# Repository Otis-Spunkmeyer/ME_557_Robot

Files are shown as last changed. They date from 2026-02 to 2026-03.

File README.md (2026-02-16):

# ME557 Robot

This repository is split into two separate top-level structures:

- Online version (ROS2 + MoveIt): `online/`
- Offline version (Arduino playback): `offline/`

## Online Version

The online stack uses ROS2/MoveIt packages for planning and control:

- `online/src/me557_pen_description`
- `online/src/me557_pen_moveit_config`
- `online/cad/`

## Offline Version

The offline stack runs trajectory playback on Arduino without ROS at runtime:

- `offline/arduino/me557_pen_arduino_ws/me557_pen_arduino_ws.ino`
- `offline/arduino/me557_pen_arduino_ws/ace_trajectory_data.h`
- `offline/arduino/README.md`
- `offline/tools/`

## Quick Start

Build online workspace:

```bash
cd online
source /opt/ros/humble/setup.bash
colcon build
```

Generate offline trajectory header:

```bash
offline/tools/export_offline_ace.sh
```

This export path uses MoveIt planning (`write_ace`) and applies configured
PlanningScene collision objects before planning.

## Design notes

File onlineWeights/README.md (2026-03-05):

# ME557 OnlineWeights — 555 Trajectory Workflow

This workspace is now **555-only** (fixed-speed playback from `trajectory_data.h`).

## Workflow

1. Launch ROS 2 / MoveIt stack:

```bash
cd /home/rosubu/ME_557_Robot/onlineWeights
./launch_rviz.sh
```

2. Trigger planning and export trajectory header:

```bash
cd /home/rosubu/ME_557_Robot/onlineWeights
./trigger_write.sh
```

Each run calls `/board_writer/run_plan` and updates:

- `robotMovements/trajectory_data.h`

3. Flash Arduino sketch:

- `robotMovements/robotMovements.ino`

4. Run from Serial Monitor at `1000000` baud:

- `555` → play `trajectory_data.h`

## Notes

- `pause` flags in `trajectory_data.h` are honored by firmware:
  - `pause=1`: full stop + contact dwell
  - `pause=2`: full stop (corner settle), no dwell
  - `pause=3`: full stop + user pause dwell
- Current firmware uses synchronized Dynamixel start (`REG_WRITE + ACTION`) for better multi-joint coordination.

## Key files

- `robotMovements/robotMovements.ino`
- `robotMovements/trajectory_data.h`
- `src/me557_pen_description/me557_pen_description/write_on_board.py`
- `src/me557_pen_moveit_config/config/write_on_board.yaml`

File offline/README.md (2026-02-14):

# ME557 Offline (Arduino)

This folder is the offline workspace.

Key paths:

- `arduino/` firmware and trajectory header.
- `tools/` export and calibration scripts.
- `individualMove.ino` helper sketch.

Entry guide:

- `arduino/README.md`

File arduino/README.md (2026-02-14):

# ME557 Arduino Offline Playback

This folder runs the pen path on Arduino without ROS at runtime.

## Files

- `me557_pen_arduino_ws/me557_pen_arduino_ws.ino`: main firmware.
- `me557_pen_arduino_ws/ace_trajectory_data.h`: exported MoveIt trajectory points.
- `../tools/export_moveit_joint_trajectory.py`: captures trajectory from MoveIt and writes header.
- `../tools/compute_moveit_calibration.py`: computes `MOVEIT_HOME_RAD` and `MOVEIT_DIR_SIGN`.

## Export ACE trajectory

From workspace root (`ME557_pen_arduino_ws`) with MoveIt running:

```bash
source /opt/ros/humble/setup.bash
source install/setup.bash
ROS_DOMAIN_ID=57 ROS_LOCALHOST_ONLY=1 \
python3 tools/export_moveit_joint_trajectory.py \
  --run-write-ace \
  --output arduino/me557_pen_arduino_ws/ace_trajectory_data.h
```

One-command offline export (launches MoveIt, exports, validates summary, then stops):

```bash
tools/export_offline_ace.sh
```

Useful options:

```bash
# Strict 14" x 14" tip bounds on XZ
tools/export_offline_ace.sh \
  --workspace-enforce-x-bounds true \
  --workspace-x-min -0.1778 \
  --workspace-x-max 0.1778 \
  --workspace-z-min 0.0 \
  --workspace-z-max 0.3556

# Floor-only Z constraint, unbounded X for tip requests
tools/export_offline_ace.sh \
  --workspace-enforce-x-bounds false \
  --workspace-z-min 0.0 \
  --workspace-z-max 10.0
```

## Arduino commands

- `555`: play exported trajectory.
- `777`: per-joint ROM sweep.
- `888`: full ROM showcase.
- `901`: print current logical/physical angles and estimated MoveIt radians.
- `902`: per-joint sign/home calibration helper.

## Calibration example

1. Send `901` and record logical angles for IDs `[1,2,4,5,6]`.
2. Send `902` for each MoveIt joint index `1..5`, choose sign direction.
3. Collect synchronized values from one pose:

- MoveIt rad (5 joints), example:
```text
0.00698 5.55596 -0.66950 0.18387 0.00524
```
- Logical deg from `901`, example:
```text
180.4 179.2 181.1 179.7 180.3
```
- Signs from `902`, example:
```text
1 1 -1 1 1
```

4. Compute constants:

```bash
python3 tools/compute_moveit_calibration.py \
  --moveit-rad 0.00698 5.55596 -0.66950 0.18387 0.00524 \
  --logical-deg 180.4 179.2 181.1 179.7 180.3 \
  --sign 1 1 -1 1 1
```

5. Paste output into `me557_pen_arduino_ws/me557_pen_arduino_ws.ino` and reflash.

## Notes

- `901` and `902` print values only; they do not save to EEPROM or source.
- Keep MoveIt and hardware values from the same pose.
- If one joint is inverted, flip only that joint sign and recompute home.

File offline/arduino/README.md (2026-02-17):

# ME557 Arduino Offline Playback

This folder is the offline ME557 firmware and trajectory data.

Repository layout:

- `online/`: ROS2 + MoveIt workspace.
- `offline/`: Arduino firmware plus offline export/calibration tools.

## Files

- `me557_pen_arduino_ws/me557_pen_arduino_ws.ino`: main firmware.
- `me557_pen_arduino_ws/ace_trajectory_data.h`: exported MoveIt trajectory points.
- `../tools/export_moveit_joint_trajectory.py`: captures trajectory from MoveIt and writes header.
- `../tools/compute_moveit_calibration.py`: computes `MOVEIT_HOME_RAD` and `MOVEIT_DIR_SIGN`.
- `../tools/generate_offline_ace_ik_trajectory.py`: legacy IK-only debug exporter (no collision-aware planning).

## Export ACE trajectory

From repo root (`ME557_pen_arduino_ws`) with online workspace already built:

```bash
source /opt/ros/humble/setup.bash
source online/install/setup.bash
ROS_DOMAIN_ID=57 ROS_LOCALHOST_ONLY=1 \
python3 offline/tools/export_moveit_joint_trajectory.py \
  --run-write-ace \
  --output offline/arduino/me557_pen_arduino_ws/ace_trajectory_data.h
```

One-command offline export (launches MoveIt, exports, validates summary, then stops):

```bash
offline/tools/export_offline_ace.sh
```

`export_offline_ace.sh` runs `write_ace` in plan-only mode, captures planned
time-parameterized joint motion, and applies configured PlanningScene collision
objects (board/table) before planning.

Useful options:

```bash
# Strict 14" x 14" tip bounds on XZ
offline/tools/export_offline_ace.sh \
  --workspace-enforce-x-bounds true \
  --workspace-x-min -0.1778 \
  --workspace-x-max 0.1778 \
  --workspace-z-min 0.0 \
  --workspace-z-max 0.3556

# Floor-only Z constraint, unbounded X for tip requests
offline/tools/export_offline_ace.sh \
  --workspace-enforce-x-bounds false \
  --workspace-z-min 0.0 \
  --workspace-z-max 10.0

# Override board collision object used by planning scene setup
offline/tools/export_offline_ace.sh \
  --scene-board-center-x 0.415 \
  --scene-board-center-y 0.000 \
  --scene-board-center-z 0.230 \
  --scene-board-size-x 0.01 \
  --scene-board-size-y 0.45 \
  --scene-board-size-z 0.42

# Rotate ACE path in board plane (+90 deg CCW about Z)
offline/tools/export_offline_ace.sh \
  --semantic-yaw-deg 90.0
```

## Arduino commands

- `555`: play exported trajectory.
- `777`: per-joint ROM sweep.
- `888`: full ROM showcase.
- `901`: print current logical/physical angles and estimated MoveIt radians.
- `902`: per-joint sign/home calibration helper.

## Calibration example

1. Send `901` and record logical angles for IDs `[1,2,4,5,6]`.
2. Send `902` for each MoveIt joint index `1..5`, choose sign direction.
3. Collect synchronized values from one pose:

- MoveIt rad (5 joints), example:
```text
0.00698 5.55596 -0.66950 0.18387 0.00524
```
- Logical deg from `901`, example:
```text
180.4 179.2 181.1 179.7 180.3
```
- Signs from `902`, example:
```text
1 1 -1 1 1
```

4. Compute constants:

```bash
python3 offline/tools/compute_moveit_calibration.py \
  --moveit-rad 0.00698 5.55596 -0.66950 0.18387 0.00524 \
  --logical-deg 180.4 179.2 181.1 179.7 180.3 \
  --sign 1 1 -1 1 1
```

5. Paste output into `me557_pen_arduino_ws/me557_pen_arduino_ws.ino` and reflash.

## Notes

- `901` and `902` print values only; they do not save to EEPROM or source.
- Keep MoveIt and hardware values from the same pose.
- If one joint is inverted, flip only that joint sign and recompute home.

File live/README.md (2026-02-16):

# ME557 Online (ROS2 + MoveIt)

This folder is the online workspace.

Key paths:

- `src/me557_pen_description`
- `src/me557_pen_moveit_config`
- `cad/`

Build and run:

```bash
cd online
source /opt/ros/humble/setup.bash
colcon build
source install/setup.bash
ros2 launch me557_pen_moveit_config demo.launch.py
```

Run `write_ace` online with the same PlanningScene collision setup used by offline export:

```bash
ros2 launch me557_pen_moveit_config write_ace_online.launch.py use_rviz:=false
```

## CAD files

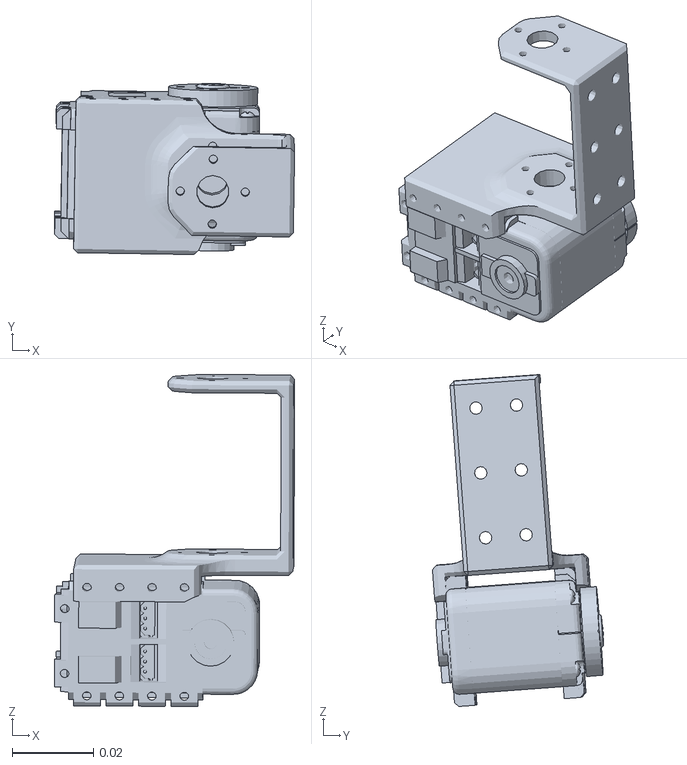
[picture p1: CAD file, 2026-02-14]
live/cad/Robot Assembly.SLDASM/meshes/Link4_Wr.STL
0.0591 x 0.0421 x 0.0817

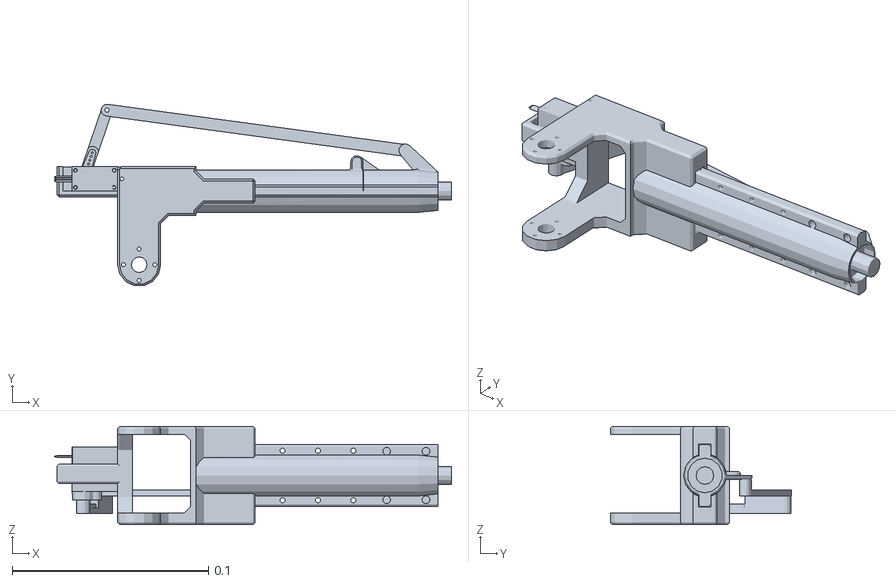
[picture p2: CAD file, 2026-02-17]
onlineWeights/src/me557_pen_description/meshes/Link6.STL
0.202 x 0.0924 x 0.05

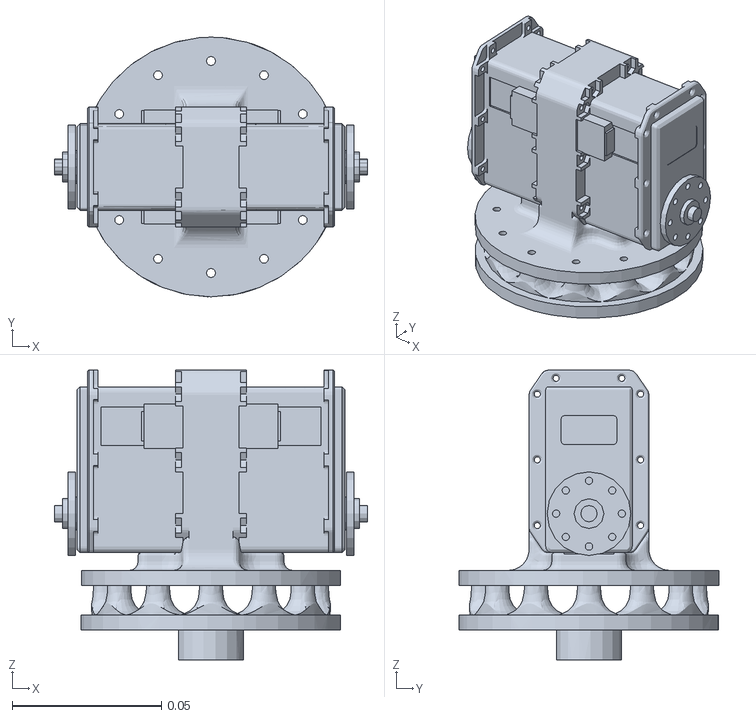
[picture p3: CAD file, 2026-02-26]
simple_with_weights_v1/meshes/RotatingBaseLink.STL
0.105 x 0.087 x 0.0971

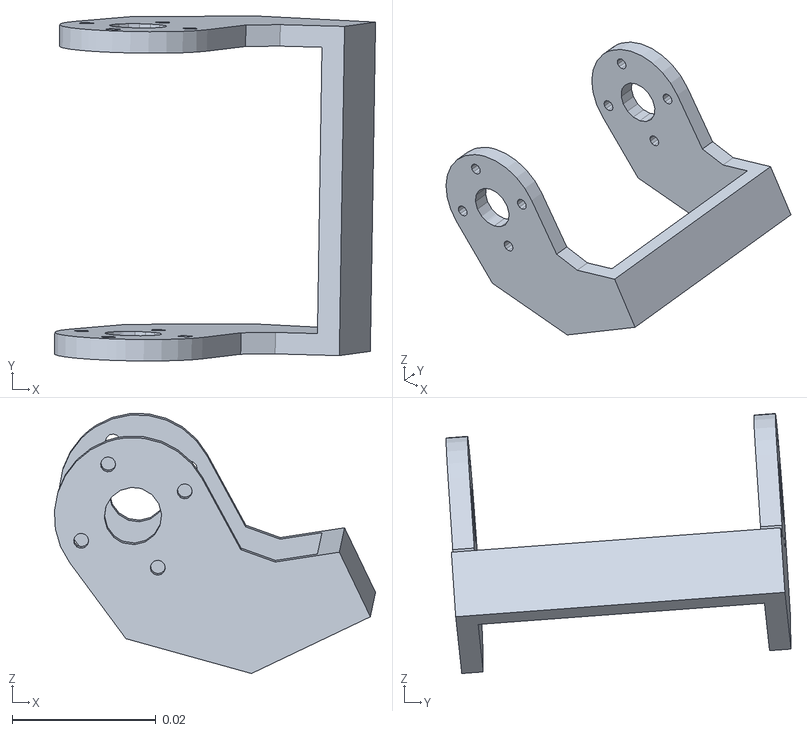
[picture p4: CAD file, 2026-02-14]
live/cad/Robot Assembly.SLDASM/meshes/Link5_EE.STL
0.0447 x 0.0481 x 0.0362

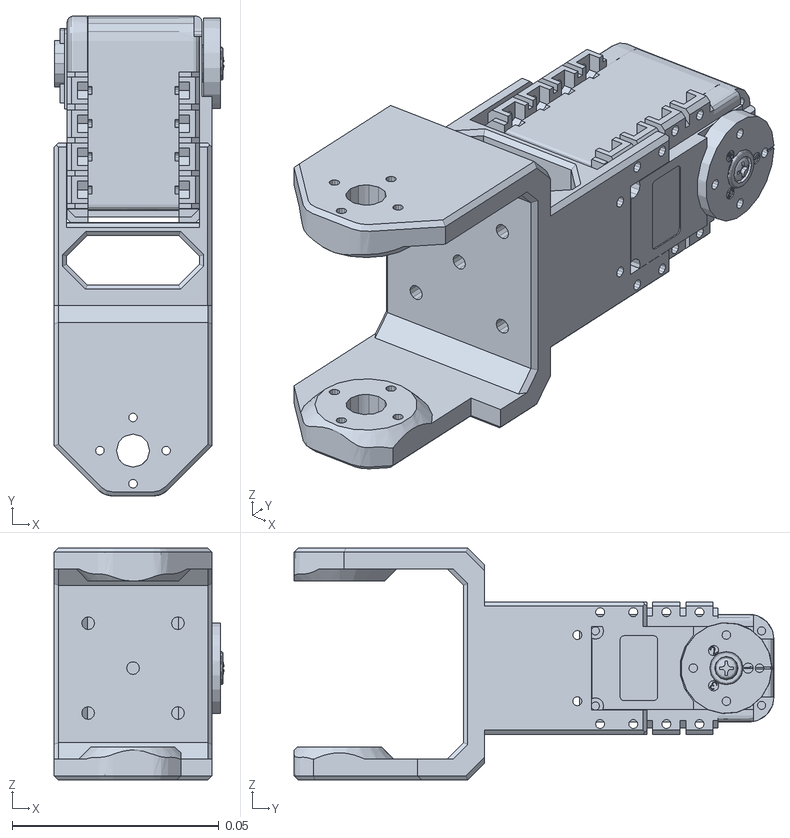
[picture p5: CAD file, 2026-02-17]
onlineWeights/src/me557_pen_description/meshes/Link4.STL
0.041 x 0.116 x 0.056

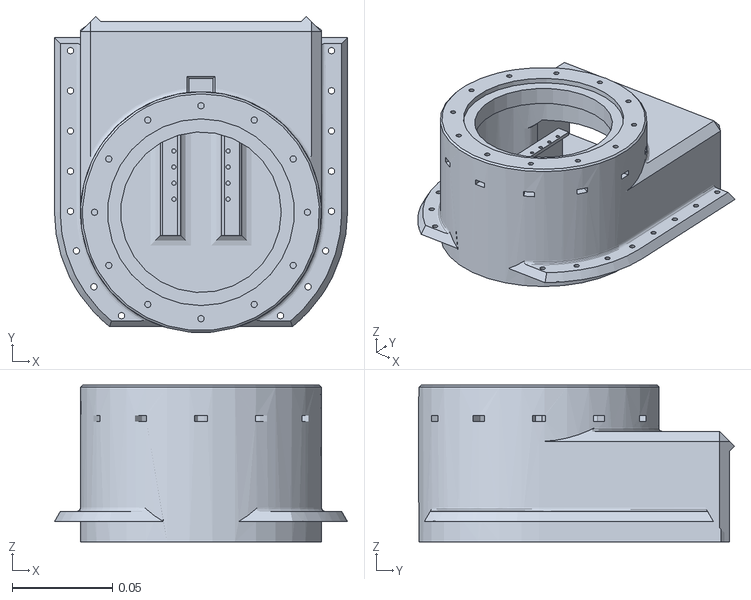
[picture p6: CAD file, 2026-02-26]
simple_with_weights_v1/meshes/FixedBase.STL
0.146 x 0.157 x 0.078

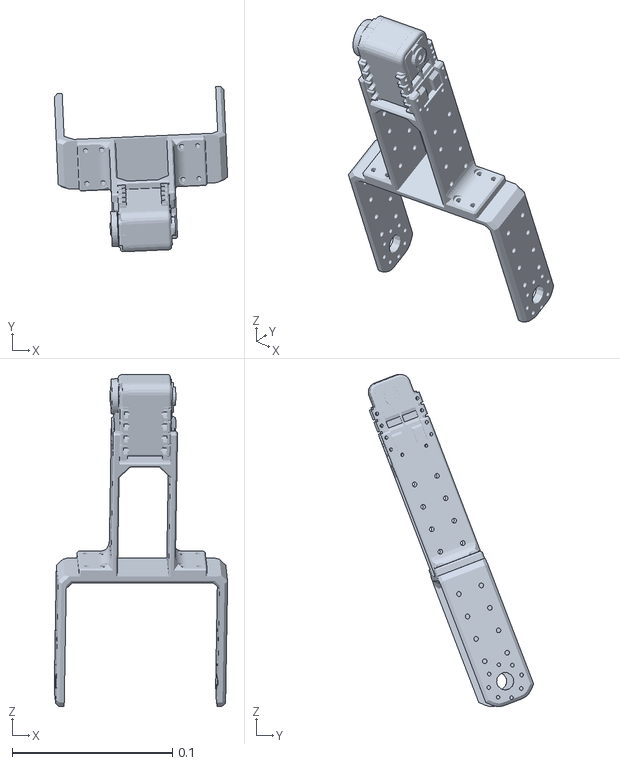
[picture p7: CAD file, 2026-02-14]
live/cad/Robot Assembly.SLDASM/meshes/Link2_R.STL
0.108 x 0.103 x 0.207

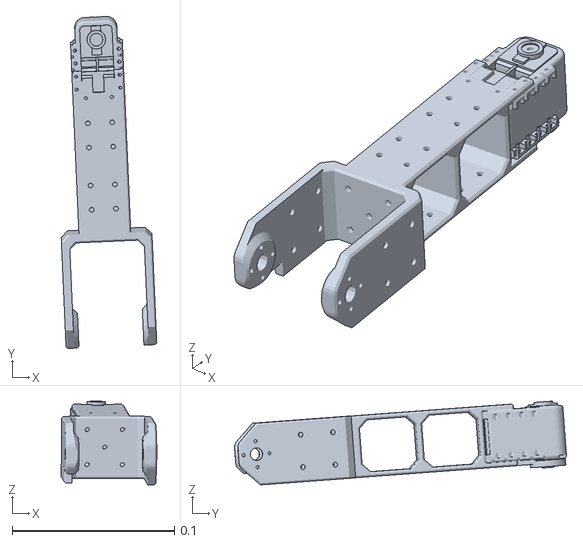
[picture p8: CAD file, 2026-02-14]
live/cad/Robot Assembly.SLDASM/meshes/Link3_Elb.STL
0.0589 x 0.205 x 0.0517

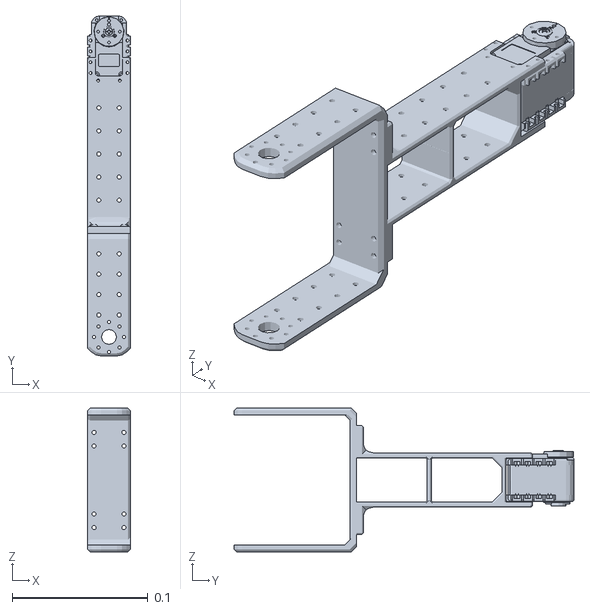
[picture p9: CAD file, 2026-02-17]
onlineWeights/src/me557_pen_description/meshes/Link3_R.STL
0.032 x 0.25 x 0.106

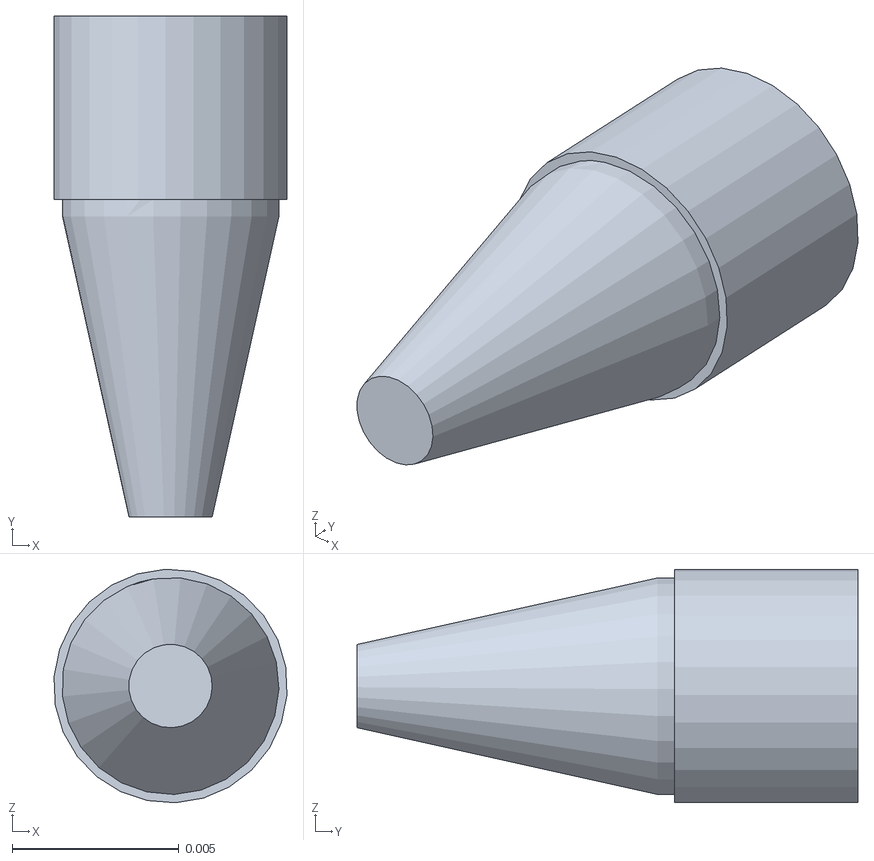
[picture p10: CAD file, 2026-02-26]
simple_with_weights_v1/meshes/PenTipLink.STL
0.00698 x 0.015 x 0.00699

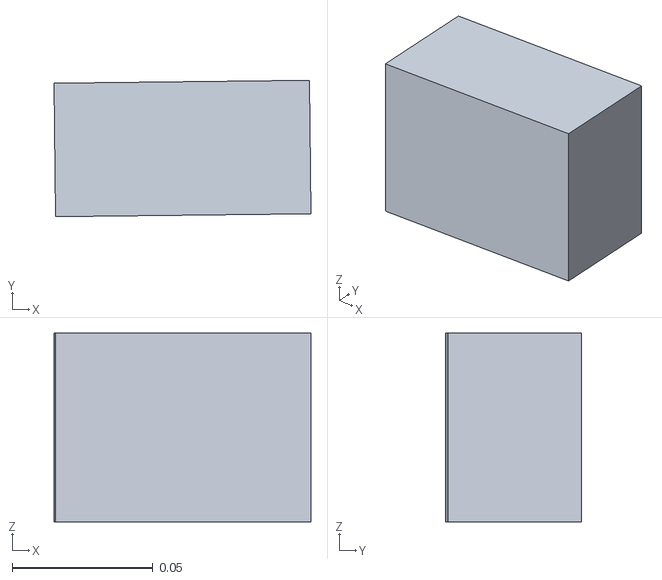
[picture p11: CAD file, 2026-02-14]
live/cad/Robot Assembly.SLDASM/meshes/Link1.STL
0.0915 x 0.0485 x 0.0671

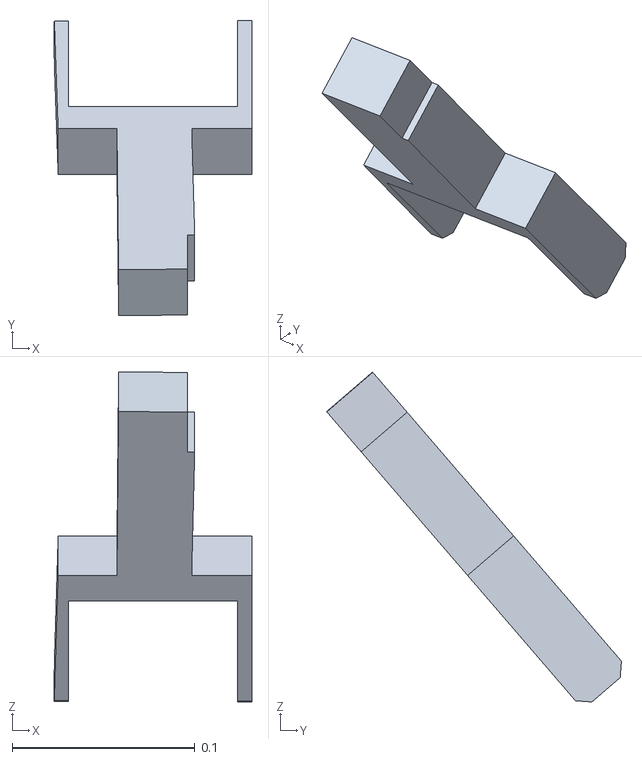
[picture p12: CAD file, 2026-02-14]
live/cad/Robot Assembly.SLDASM/meshes/Link2_L.STL
0.108 x 0.161 x 0.181

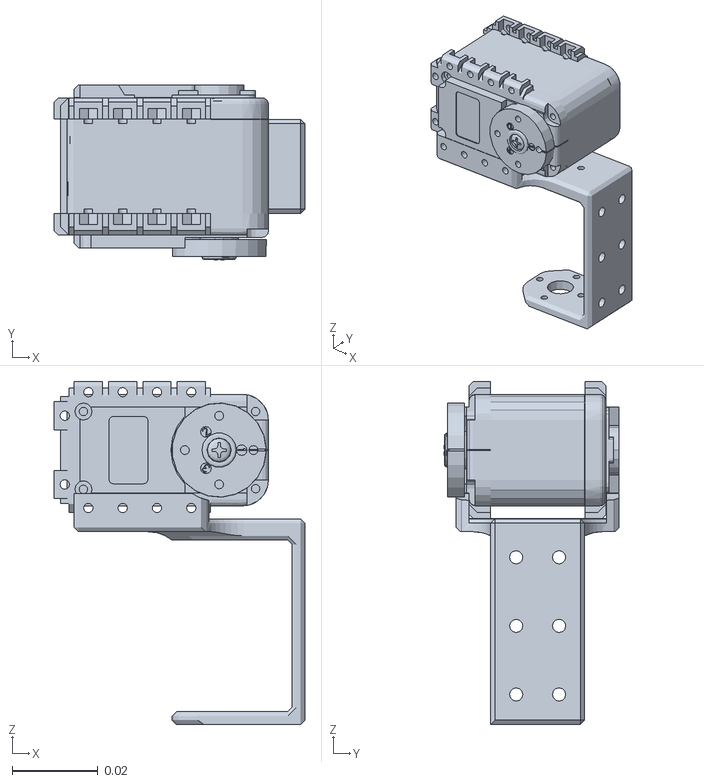
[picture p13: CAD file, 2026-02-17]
onlineWeights/src/me557_pen_description/meshes/Link5.STL
0.0585 x 0.0409 x 0.08

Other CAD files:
onlineWeights/src/me557_pen_description/meshes/Link1.STL
simple_with_weights_v1/meshes/ElbowLink.STL
simple_with_weights_v1/meshes/PenLink.STL
simple_with_weights_v1/meshes/WristLink.STL
live/cad/Robot Assembly.SLDASM/meshes/Link4.STL
live/cad/Robot Assembly.SLDASM/meshes/Link5.STL
live/cad/Robot Assembly.SLDASM/meshes/Link6.STL
live/cad/Robot Assembly.SLDASM/meshes/Pen_tip.STL
live/cad/Robot Assembly.SLDASM/meshes/base_link.STL
onlineWeights/src/me557_pen_description/meshes/Pen_tip.STL
onlineWeights/src/me557_pen_description/meshes/base_link.STL
simple_with_weights_v1/meshes/ShoulderLink.STL

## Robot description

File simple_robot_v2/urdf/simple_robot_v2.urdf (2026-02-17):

<?xml version="1.0" encoding="utf-8"?>
<!-- This URDF was automatically created by SolidWorks to URDF Exporter! Originally created by Stephen Brawner (brawner@gmail.com) 
     Commit Version: 1.6.0-4-g7f85cfe  Build Version: 1.6.7995.38578
     For more information, please see http://wiki.ros.org/sw_urdf_exporter -->
<robot name="simple_robot_v2">
  <link name="FixedBase">
    <inertial>
      <origin xyz="-0.008662 6.915E-09 0.034203" rpy="0 0 0" />
      <mass value="0.49574" />
      <inertia ixx="0.0011079" ixy="1.4362E-10" ixz="-3.7324E-05" iyy="0.0011344" iyz="-8.7399E-11" izz="0.0016547" />
    </inertial>
    <visual>
      <origin xyz="0 0 0" rpy="0 0 0" />
      <geometry>
        <mesh filename="package://simple_robot_v2/meshes/FixedBase.STL" />
      </geometry>
      <material name="">
        <color rgba="0.79216 0.81961 0.93333 1" />
      </material>
    </visual>
    <collision>
      <origin xyz="0 0 0" rpy="0 0 0" />
      <geometry>
        <mesh filename="package://simple_robot_v2/meshes/FixedBase.STL" />
      </geometry>
    </collision>
  </link>
  <link name="RotatingBaseLink">
    <inertial>
      <origin xyz="-1.0615E-08 1.3952E-09 0.05044" rpy="0 0 0" />
      <mass value="0.24905" />
      <inertia ixx="0.00030195" ixy="6.1355E-07" ixz="2.7299E-11" iyy="0.0002068" iyz="4.0363E-11" izz="0.00019603" />
    </inertial>
    <visual>
      <origin xyz="0 0 0" rpy="0 0 0" />
      <geometry>
        <mesh filename="package://simple_robot_v2/meshes/RotatingBaseLink.STL" />
      </geometry>
      <material name="">
        <color rgba="0.50196 0.50196 1 1" />
      </material>
    </visual>
    <collision>
      <origin xyz="0 0 0" rpy="0 0 0" />
      <geometry>
        <mesh filename="package://simple_robot_v2/meshes/RotatingBaseLink.STL" />
      </geometry>
    </collision>
  </link>
  <joint name="RotatingBaseJoint" type="revolute">
    <origin xyz="0 0 0.05" rpy="0 0 0" />
    <parent link="FixedBase" />
    <child link="RotatingBaseLink" />
    <axis xyz="0 0 -1" />
    <limit lower="2.0944" upper="3.8397" effort="0" velocity="0" />
  </joint>
  <link name="ShoulderLink">
    <inertial>
      <origin xyz="1.5118E-06 0.13231 0.0003468" rpy="0 0 0" />
      <mass value="0.12701" />
      <inertia ixx="0.00076308" ixy="1.1682E-08" ixz="8.706E-09" iyy="0.00010667" iyz="-3.3149E-06" izz="0.00067538" />
    </inertial>
    <visual>
      <origin xyz="0 0 0" rpy="0 0 0" />
      <geometry>
        <mesh filename="package://simple_robot_v2/meshes/ShoulderLink.STL" />
      </geometry>
      <material name="">
        <color rgba="0.79216 0.81961 0.93333 1" />
      </material>
    </visual>
    <collision>
      <origin xyz="0 0 0" rpy="0 0 0" />
      <geometry>
        <mesh filename="package://simple_robot_v2/meshes/ShoulderLink.STL" />
      </geometry>
    </collision>
  </link>
  <joint name="ShoulderJoint" type="revolute">
    <origin xyz="0 0 0.049" rpy="1.5708 0 0.0064475" />
    <parent link="RotatingBaseLink" />
    <child link="ShoulderLink" />
    <axis xyz="0 0 1" />
    <limit lower="2.0944" upper="4.18879" effort="0" velocity="0" />
  </joint>
  <link name="ElbowLink">
    <inertial>
      <origin xyz="0.00036697 0.055834 -0.0004101" rpy="0 0 0" />
      <mass value="0.083206" />
      <inertia ixx="9.1587E-05" ixy="-1.7788E-06" ixz="-2.7941E-07" iyy="2.5642E-05" iyz="2.0881E-06" izz="8.5875E-05" />
    </inertial>
    <visual>
      <origin xyz="0 0 0" rpy="0 0 0" />
      <geometry>
        <mesh filename="package://simple_robot_v2/meshes/ElbowLink.STL" />
      </geometry>
      <material name="">
        <color rgba="0.79216 0.81961 0.93333 1" />
      </material>
    </visual>
    <collision>
      <origin xyz="0 0 0" rpy="0 0 0" />
      <geometry>
        <mesh filename="package://simple_robot_v2/meshes/ElbowLink.STL" />
      </geometry>
    </collision>
  </link>
  <joint name="ElbowJoint" type="revolute">
    <origin xyz="0 0.2247 0.00104" rpy="0 0 0" />
    <parent link="ShoulderLink" />
    <child link="ElbowLink" />
    <axis xyz="0 0 1" />
    <limit lower="1.309" upper="5.06145" effort="0" velocity="0" />
  </joint>
  <link name="WristLink">
    <inertial>
      <origin xyz="-0.010184 -0.0007354 0.034941" rpy="0 0 0" />
      <mass value="0.053757" />
      <inertia ixx="1.8975E-05" ixy="3.4773E-08" ixz="4.7677E-06" iyy="2.5817E-05" iyz="2.3142E-07" izz="1.7812E-05" />
    </inertial>
    <visual>
      <origin xyz="0 0 0" rpy="0 0 0" />
      <geometry>
        <mesh filename="package://simple_robot_v2/meshes/WristLink.STL" />
      </geometry>
      <material name="">
        <color rgba="0.9098 0.44314 0.031373 1" />
      </material>
    </visual>
    <collision>
      <origin xyz="0 0 0" rpy="0 0 0" />
      <geometry>
        <mesh filename="package://simple_robot_v2/meshes/WristLink.STL" />
      </geometry>
    </collision>
  </link>
  <joint name="WristJoint" type="revolute">
    <origin xyz="0.00108 0.0935 -0.001" rpy="1.5708 0 1.5708" />
    <parent link="ElbowLink" />
    <child link="WristLink" />
    <axis xyz="0 0 -1" />
    <limit lower="2.618" upper="4.5379" effort="0" velocity="0" />
  </joint>
  <link name="PenLink">
    <inertial>
      <origin xyz="0.048807 0.037513 -0.0021456" rpy="0 0 0" />
      <mass value="0.081357" />
      <inertia ixx="2.8223E-05" ixy="-3.704E-06" ixz="-2.8914E-06" iyy="0.00024631" iyz="5.6477E-07" izz="0.00024327" />
    </inertial>
    <visual>
      <origin xyz="0 0 0" rpy="0 0 0" />
      <geometry>
        <mesh filename="package://simple_robot_v2/meshes/PenLink.STL" />
      </geometry>
      <material name="">
        <color rgba="0.50196 1 0.50196 1" />
      </material>
    </visual>
    <collision>
      <origin xyz="0 0 0" rpy="0 0 0" />
      <geometry>
        <mesh filename="package://simple_robot_v2/meshes/PenLink.STL" />
      </geometry>
    </collision>
  </link>
  <joint name="PenJoint" type="revolute">
    <origin xyz="0 -0.001 0.041" rpy="1.5708 0 0" />
    <parent link="WristLink" />
    <child link="PenLink" />
    <axis xyz="0 0 1" />
    <limit lower="1.4835" upper="3.8397" effort="0" velocity="0" />
  </joint>
  <link name="PenTipLink">
    <inertial>
      <origin xyz="1.2388E-08 -1.5096E-08 -0.0095156" rpy="0 0 0" />
      <mass value="0.00038082" />
      <inertia ixx="6.068E-09" ixy="2.1976E-14" ixz="1.8806E-14" iyy="6.0679E-09" iyz="-2.2912E-14" izz="1.8923E-09" />
    </inertial>
    <visual>
      <origin xyz="0 0 0" rpy="0 0 0" />
      <geometry>
        <mesh filename="package://simple_robot_v2/meshes/PenTipLink.STL" />
      </geometry>
      <material name="">
        <color rgba="0.50196 1 0.50196 1" />
      </material>
    </visual>
    <collision>
      <origin xyz="0 0 0" rpy="0 0 0" />
      <geometry>
        <mesh filename="package://simple_robot_v2/meshes/PenTipLink.STL" />
      </geometry>
    </collision>
  </link>
  <joint name="PenTipJoint" type="continuous">
    <origin xyz="0.17403 0.0375 -0.00098" rpy="1.5708 -1.5643 1.5708" />
    <parent link="PenLink" />
    <child link="PenTipLink" />
    <axis xyz="-0.45244 0.63071 -0.63047" />
  </joint>
</robot>

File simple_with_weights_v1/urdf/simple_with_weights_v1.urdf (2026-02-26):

<?xml version="1.0" encoding="utf-8"?>
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
<robot name="simple_with_weights_v1">
  <link name="FixedBase">
    <inertial>
      <origin xyz="6.915E-09 0.008662 0.034203" rpy="0 0 0" />
      <mass value="0.49574" />
      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
    </inertial>
    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
  </link>
  <link name="RotatingBaseLink">
    <inertial>
      <origin xyz="1.7639E-09 1.0285E-08 0.05044" rpy="0 0 0" />
      <mass value="0.36361" />
      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
    </inertial>
    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
  </link>
  <joint name="RotatingBaseJoint" type="revolute">
    <origin xyz="0 0 0.05" rpy="0 0 0" />
    <parent link="FixedBase" />
    <child link="RotatingBaseLink" />
    <axis xyz="0 0 -1" />
    <limit lower="0" upper="0" effort="0.15" velocity="0" />
  </joint>
  <link name="ShoulderLink">
    <inertial>
      <origin xyz="-0.000346804399082955 -1.51178301074372E-06 0.132307785392207" rpy="0 0 0" />
      <mass value="0.138435482736122" />
      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
    </inertial>
    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
  </link>
  <joint name="ShoulderJoint" type="revolute">
    <origin xyz="0 0 0.049" rpy="0 0 0" />
    <parent link="RotatingBaseLink" />
    <child link="ShoulderLink" />
    <axis xyz="-1 0 0" />
    <limit lower="0" upper="0" effort="8" velocity="0" />
  </joint>
  <link name="ElbowLink">
    <inertial>
      <origin xyz="0.000410096249429826 -0.000366974946254552 0.0558340165515793" rpy="0 0 0" />
      <mass value="0.0915265999893292" />
      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
    </inertial>
    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
  </link>
  <joint name="ElbowJoint" type="revolute">
    <origin xyz="-0.00104 0 0.2247" rpy="0 0 0" />
    <parent link="ShoulderLink" />
    <child link="ElbowLink" />
    <axis xyz="-1 0 0" />
    <limit lower="0" upper="0" effort="0.15" velocity="0" />
  </joint>
  <link name="WristLink">
    <inertial>
      <origin xyz="0.00073541 -0.034941 -0.010184" rpy="0 0 0" />
      <mass value="0.069884" />
      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
    </inertial>
    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
  </link>
  <joint name="WristJoint" type="revolute">
    <origin xyz="0.001 -0.00108 0.0935" rpy="0 0 0" />
    <parent link="ElbowLink" />
    <child link="WristLink" />
    <axis xyz="0 1 0" />
    <limit lower="0" upper="0" effort="0.15" velocity="0" />
  </joint>
  <link name="PenLink">
    <inertial>
      <origin xyz="-0.0021456 -0.037513 0.048807" rpy="0 0 0" />
      <mass value="0.071594" />
      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
    </inertial>
    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
  </link>
  <joint name="PenJoint" type="revolute">
    <origin xyz="0.001 -0.041 0" rpy="0 0 0" />
    <parent link="WristLink" />
    <child link="PenLink" />
    <axis xyz="1 0 0" />
    <limit lower="0" upper="0" effort="0.15" velocity="0" />
  </joint>
  <link name="PenTipLink">
    <inertial>
      <origin xyz="-1.2671E-08 0.0095156 1.4864E-08" rpy="0 0 0" />
      <mass value="0.00049506" />
      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
    </inertial>
    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
  </link>
  <joint name="PenTipJoint" type="continuous">
    <origin xyz="-0.00098 -0.0375 0.17403" rpy="-1.5708 0 -0.5042" />
    <parent link="PenLink" />
    <child link="PenTipLink" />
    <axis xyz="-0.70084 0.63047 0.33365" />
  </joint>
</robot>

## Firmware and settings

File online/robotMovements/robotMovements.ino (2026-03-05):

#include <Dynamixel2Arduino.h>
#include <Servo.h>
#include "trajectory_data.h"
#include "moveItData.h"

#define DXL_SERIAL Serial1
#define PC_SERIAL  Serial

using namespace ControlTableItem;

Dynamixel2Arduino d2a(DXL_SERIAL);

// PWM hobby servo on pin 3 — controlled as ID 7
#define PEN_SERVO_PIN      3
#define PEN_SERVO_HOME_DEG 90
Servo penServo;

// =============================================================================
// CONFIGURATION — edit these values to tune robot behaviour
// =============================================================================
const int   HOME_SPEED         = 15;    // Speed when homing (seq 100 / startup)
const int   MANUAL_SPEED       = 15;    // Speed in manual ID control mode
const int   TRAJECTORY_SPEED   = 8;     // Speed during trajectory streaming — slow so moves take LONGER than the interval
const int   ACCEL_SMOOTH       = 15;    // Profile acceleration — moderate ramp, allows smooth blending

// Trajectory playback
// During a drawing segment keyframes are STREAMED at this interval.  The servo
// receives the next goal position while still moving toward the previous one;
// its internal velocity profile blends smoothly through each waypoint.
// Tune so the interval roughly matches how long each inter-keyframe move takes
// at TRAJECTORY_SPEED — too short and servos lag; too long and they over-stop.
const unsigned long  KEYFRAME_INTERVAL_MS = 30;  // ms between streamed keyframes
// Extra settle time (ms) after all servos report stopped at a pause boundary.
const unsigned long  SETTLE_MS            = 50;
// Dwell time (ms) applied at draw<->travel boundary keyframes (pause flag).
const unsigned long  RETRACT_PAUSE_MS     = 500;
// Timeout (ms) for waitForMotionComplete — safety valve so a stalled servo
// does not hang the sketch forever.
const unsigned long  MOTION_TIMEOUT_MS    = 8000;

// Per-servo PID overrides for servo 1 (base rotation).
// This servo has an extra bearing load causing overshoot oscillation.
// Lowering P reduces the aggressiveness of correction (less overshoot).
// Adding D adds velocity-based damping that actively kills oscillation.
// These only apply to XM/XH servos; AX-12 uses compliance slope instead.
//   XM/XH defaults: P=800, I=0, D=0
//   AX-12: compliance slope used instead (see applySmoothing)
const int SERVO1_P_GAIN          = 400;   // < 800 default: reduce overshoot aggressiveness
const int SERVO1_D_GAIN          = 400;   // > 0 default: add damping to kill oscillation
const int SERVO1_I_GAIN          = 0;     // keep at 0 — I gain adds wind-up, worsens oscillation
const int SERVO1_AX12_SLOPE      = 96;    // AX-12 only: softer compliance = less oscillation

// Per-servo compliance overrides for servo 4 (AX-12 with worst moment arm).
// High load at a disadvantaged moment arm causes the servo to hunt:
// it overshoots slightly, brakes, overshoots the other way, repeat.
//
// Slope controls the torque ramp around the target (higher = softer spring).
//   Valid values: 2, 4, 8, 16, 32, 64, 128
//   Higher slope = gentler approach = less snap-back jitter, but slightly
//   less positional stiffness.  Start at 128 and tighten down if needed.
//
// Margin is the dead-zone (raw units) where zero torque is applied.
//   0 = fight every tiny error (causes buzzing under load)
//   2-4 = ignore sub-degree noise (stops the hunting loop)
//   Don't go above ~5 or positional accuracy visibly degrades.
const int SERVO4_AX12_SLOPE          = 64;  // middle ground: fast enough, soft enough
const int SERVO4_AX12_MARGIN         = 3;   // wider dead-zone kills resonance-exciting micro-hunt
// Servo 4 gets its own trajectory speed, higher than the global setting.
// At speed 8 it lacks torque authority against gravity when the arm is
// extended — the joint lags, then snaps/bounces to catch up.
// A higher speed keeps torque output high enough to move decisively.
const int SERVO4_TRAJECTORY_SPEED    = 15;
// =============================================================================

// Per-motor calibration, mapping physical to logical angle ranges and offsets
struct RobotMotor {
  uint8_t  id;            // Dynamixel ID
  float    physicalOffset; // Physical zero offset used to align to logical 180deg
  float    lowerLimit;    // Logical lower limit (deg)
  float    upperLimit;    // Logical upper limit (deg)
  uint16_t modelNumber;   // Cached on first use — avoids a bus read every move
};

RobotMotor motors[] = {
  {1, 150.0, 120.0, 220.0, 0},
  {2, 170.0, 120.0, 240.0, 0},  // MX-64A — Protocol 1.0, model 310
  {3, 187.0, 120.0, 240.0, 0},  // MX-64A — Protocol 1.0, model 310
  {4, 150.0,  40.0, 240.0, 0},
  {5, 150.0, 100.0, 260.0, 0},
  {6, 150.0, 140.0, 300.0, 0}
};


const uint8_t MOVEIT_TO_SERVO_ID[5] = {1, 2, 4, 5, 6};

// MoveIt (radians) <-> logical (degrees) calibration.
// Tune once on hardware; keep consistent with the MoveIt export tool.
const float MOVEIT_HOME_RAD[5] = {0.0f, 0.0f, 0.0f, 0.0f, 0.0f};
const float MOVEIT_DIR_SIGN[5] = {-1.0f, 1.0f, 1.0f, -1.0f, 1.0f};

// =============================================================================
// UTILITIES
// =============================================================================

RobotMotor* findMotor(uint8_t id) {
  for (int i = 0; i < 6; i++) {
    if (motors[i].id == id) return &motors[i];
  }
  return nullptr;
}

float rawToPhysicalDegrees(uint16_t model, int32_t raw) {
  if (model == 12) return ((float)raw) * (300.0f / 1023.0f);   // AX-12: 10-bit / 300 deg
  return ((float)raw) * (360.0f / 4095.0f);                    // XM/XH:  12-bit / 360 deg
}

float logicalToPhysical(uint8_t id, float logicalAngle) {
  RobotMotor* m = findMotor(id);
  if (!m) return logicalAngle;
  float safeLogical = constrain(logicalAngle, m->lowerLimit, m->upperLimit);
  return safeLogical + (m->physicalOffset - 180.0);
}

float physicalToLogical(uint8_t id, float physicalAngle) {
  RobotMotor* m = findMotor(id);
  if (!m) return physicalAngle;
  return physicalAngle - (m->physicalOffset - 180.0);
}

bool readPresentLogical(uint8_t id, float &logicalOut, float &physicalOut) {
  if (!d2a.ping(id)) return false;
  uint16_t model = d2a.getModelNumber(id);
  int32_t raw = d2a.readControlTableItem(PRESENT_POSITION, id);
  physicalOut = rawToPhysicalDegrees(model, raw);
  logicalOut  = physicalToLogical(id, physicalOut);
  return true;
}

float moveitRadToLogical(uint8_t idx, float rad) {
  const float RAD2DEG = 57.2957795f;
  return 180.0f + MOVEIT_DIR_SIGN[idx] * (rad - MOVEIT_HOME_RAD[idx]) * RAD2DEG;
}

// =============================================================================
// DIAGNOSTICS
// =============================================================================

// Read and print key registers for every servo so we can see exactly what
// state the hardware is in BEFORE we try to move anything.
void scanServos() {
  PC_SERIAL.println("");
  PC_SERIAL.println("=== SERVO SCAN ===");
  uint8_t ids[] = {1, 2, 3, 4, 5, 6};
  for (uint8_t id : ids) {
    PC_SERIAL.print("  ID "); PC_SERIAL.print(id); PC_SERIAL.print(": ");
    if (!d2a.ping(id)) {
      PC_SERIAL.println("NO RESPONSE (not found on bus)");
      continue;
    }
    uint16_t model = d2a.getModelNumber(id);
    PC_SERIAL.print("model="); PC_SERIAL.print(model);
    if (model == 12) {
      int32_t movSpeed = d2a.readControlTableItem(MOVING_SPEED, id);
      int32_t cwSlope  = d2a.readControlTableItem(CW_COMPLIANCE_SLOPE,  id);
      int32_t ccwSlope = d2a.readControlTableItem(CCW_COMPLIANCE_SLOPE, id);
      int32_t cwMarg   = d2a.readControlTableItem(CW_COMPLIANCE_MARGIN,  id);
      int32_t ccwMarg  = d2a.readControlTableItem(CCW_COMPLIANCE_MARGIN, id);
      PC_SERIAL.print(" (AX-12)");
      PC_SERIAL.print(" | MOVING_SPEED=");        PC_SERIAL.print(movSpeed);
      PC_SERIAL.print(" | CW_SLOPE=");            PC_SERIAL.print(cwSlope);
      PC_SERIAL.print(" | CCW_SLOPE=");           PC_SERIAL.print(ccwSlope);
      PC_SERIAL.print(" | CW_MARGIN=");           PC_SERIAL.print(cwMarg);
      PC_SERIAL.print(" | CCW_MARGIN=");          PC_SERIAL.println(ccwMarg);
    } else if (model == 310) {
      int32_t movSpeed = d2a.readControlTableItem(MOVING_SPEED,    id);
      int32_t pGain    = d2a.readControlTableItem(POSITION_P_GAIN, id);
      int32_t iGain    = d2a.readControlTableItem(POSITION_I_GAIN, id);
      int32_t dGain    = d2a.readControlTableItem(POSITION_D_GAIN, id);
      PC_SERIAL.print(" (MX-64A Proto1)");
      PC_SERIAL.print(" | MOVING_SPEED="); PC_SERIAL.print(movSpeed);
      PC_SERIAL.print(" | P_GAIN=");       PC_SERIAL.print(pGain);
      PC_SERIAL.print(" | I_GAIN=");       PC_SERIAL.print(iGain);
      PC_SERIAL.print(" | D_GAIN=");       PC_SERIAL.println(dGain);
    } else {
      int32_t opMode   = d2a.readControlTableItem(OPERATING_MODE,      id);
      int32_t profVel  = d2a.readControlTableItem(PROFILE_VELOCITY,    id);
      int32_t profAcc  = d2a.readControlTableItem(PROFILE_ACCELERATION,id);
      int32_t torqueEn = d2a.readControlTableItem(TORQUE_ENABLE,       id);
      int32_t pGain    = d2a.readControlTableItem(POSITION_P_GAIN,     id);
      int32_t dGain    = d2a.readControlTableItem(POSITION_D_GAIN,     id);
      PC_SERIAL.print(" (XM/XH)");
      PC_SERIAL.print(" | OPERATING_MODE=");      PC_SERIAL.print(opMode);
      PC_SERIAL.print(opMode == 3 ? " (Position OK)" : " *** NOT POSITION MODE ***");
      PC_SERIAL.print(" | TORQUE_ENABLE=");       PC_SERIAL.print(torqueEn);
      PC_SERIAL.print(" | PROFILE_VELOCITY=");    PC_SERIAL.print(profVel);
      PC_SERIAL.print(" | PROFILE_ACCEL=");       PC_SERIAL.print(profAcc);
      PC_SERIAL.print(" | P_GAIN=");              PC_SERIAL.print(pGain);
      PC_SERIAL.print(" | D_GAIN=");              PC_SERIAL.println(dGain);
    }
  }
  PC_SERIAL.println("=== END SCAN ===");
  PC_SERIAL.println("");
}

// =============================================================================
// MOTION
// =============================================================================

void applySmoothing(uint8_t id, uint16_t model) {
  PC_SERIAL.print("  [applySmoothing] ID="); PC_SERIAL.print(id);
  PC_SERIAL.print(" model="); PC_SERIAL.print(model);
  if (model == 12) {
    // AX-12: compliance slopes + margin
    int slope  = 32;
    int margin = 1;
    if (id == 1) { slope = SERVO1_AX12_SLOPE; }
    if (id == 4) { slope = SERVO4_AX12_SLOPE; margin = SERVO4_AX12_MARGIN; }
    d2a.writeControlTableItem(CW_COMPLIANCE_SLOPE,   id, slope);
    d2a.writeControlTableItem(CCW_COMPLIANCE_SLOPE,  id, slope);
    d2a.writeControlTableItem(CW_COMPLIANCE_MARGIN,  id, margin);
    d2a.writeControlTableItem(CCW_COMPLIANCE_MARGIN, id, margin);
    PC_SERIAL.print(" | AX-12 slope="); PC_SERIAL.print(slope);
    PC_SERIAL.print(" margin="); PC_SERIAL.println(margin);
  } else if (model == 310) {
    // MX-64A Protocol 1.0: uses PID gains + MOVING_SPEED (no compliance slopes,
    // no OPERATING_MODE register — those only exist on Protocol 2.0 servos).
    // NOTE: ControlTableItem::POSITION_P_GAIN maps to the Protocol 2.0 address
    // (80), which is wrong for MX-64A Protocol 1.0 (P gain is at address 28).
    // Leave PID at hardware defaults — they are fine for position control.
    PC_SERIAL.println(" | MX-64A Proto1 OK (default PID)");
  } else {
    // XM/XH Protocol 2.0: OPERATING_MODE + PROFILE_VELOCITY/ACCELERATION + PID
    d2a.torqueOff(id);
    d2a.writeControlTableItem(OPERATING_MODE, id, 3);
    int32_t modeReadBack = d2a.readControlTableItem(OPERATING_MODE, id);
    PC_SERIAL.print(" | Set OPERATING_MODE=3, readback="); PC_SERIAL.print(modeReadBack);
    PC_SERIAL.print(modeReadBack == 3 ? " OK" : " *** FAILED ***");
    d2a.writeControlTableItem(PROFILE_ACCELERATION, id, ACCEL_SMOOTH);
    if (id == 1) {
      d2a.writeControlTableItem(POSITION_P_GAIN, id, SERVO1_P_GAIN);
      d2a.writeControlTableItem(POSITION_D_GAIN, id, SERVO1_D_GAIN);
      d2a.writeControlTableItem(POSITION_I_GAIN, id, SERVO1_I_GAIN);
    }
    PC_SERIAL.print(" | PROFILE_ACCEL="); PC_SERIAL.println(ACCEL_SMOOTH);
  }
}

// Convert physical degrees to the servo's raw bit value.
uint16_t physicalToRaw(uint16_t model, float physicalDegrees) {
  return (model == 12)
    ? (uint16_t)(constrain(physicalDegrees, 0, 300) * (1023.0 / 300.0))
    : (uint16_t)(constrain(physicalDegrees, 0, 360) * (4095.0 / 360.0));
}

// Low-level: write speed + goal position to a servo in physical degrees.
// Used for homing and manual mode where per-call overhead is fine.
void executeMove(uint8_t id, float physicalDegrees, int speed) {
  RobotMotor* m = findMotor(id);
  if (m && m->modelNumber == 0) m->modelNumber = d2a.getModelNumber(id);
  uint16_t model = m ? m->modelNumber : d2a.getModelNumber(id);

  static bool smoothed[11] = {false};
  if (id < 11 && !smoothed[id]) {
    PC_SERIAL.print("  [executeMove] First call for ID="); PC_SERIAL.print(id);
    PC_SERIAL.println(" -> applySmoothing");
    applySmoothing(id, model);
    smoothed[id] = true;
  }

  // AX-12 (model 12) and MX-64A Protocol 1.0 (model 310) both use MOVING_SPEED.
  // XM/XH Protocol 2.0 uses PROFILE_VELOCITY.
  if (model == 12 || model == 310) {
    d2a.writeControlTableItem(MOVING_SPEED, id, speed);
    int32_t readBack = d2a.readControlTableItem(MOVING_SPEED, id);
    PC_SERIAL.print("  [executeMove] ID="); PC_SERIAL.print(id);
    PC_SERIAL.print(model == 12 ? " AX-12" : " MX-64A");
    PC_SERIAL.print(" | set MOVING_SPEED="); PC_SERIAL.print(speed);
    PC_SERIAL.print(" readback="); PC_SERIAL.print(readBack);
    PC_SERIAL.print(" | goal_phys="); PC_SERIAL.println(physicalDegrees, 1);
  } else {
    d2a.writeControlTableItem(PROFILE_VELOCITY, id, speed);
    int32_t readBack = d2a.readControlTableItem(PROFILE_VELOCITY, id);
    PC_SERIAL.print("  [executeMove] ID="); PC_SERIAL.print(id);
    PC_SERIAL.print(" XM/XH | set PROFILE_VELOCITY="); PC_SERIAL.print(speed);
    PC_SERIAL.print(" readback="); PC_SERIAL.print(readBack);
    PC_SERIAL.print(" | goal_phys="); PC_SERIAL.println(physicalDegrees, 1);
  }
  d2a.torqueOn(id);
  d2a.setGoalPosition(id, physicalToRaw(model, physicalDegrees));
}

// Prepare all servos for trajectory playback: apply smoothing, set speed, and
// enable torque ONCE. During playback only bare goal-position writes are sent,
// so all joints get their commands as close together as possible.
void prepareServosForTrajectory() {
  uint8_t allIds[] = {1, 2, 3, 4, 5, 6};
  for (uint8_t id : allIds) {
    RobotMotor* m = findMotor(id);
    if (m && m->modelNumber == 0) m->modelNumber = d2a.getModelNumber(id);
    uint16_t model = m ? m->modelNumber : d2a.getModelNumber(id);
    applySmoothing(id, model);
    int spd = (id == 4) ? SERVO4_TRAJECTORY_SPEED : TRAJECTORY_SPEED;
    if (model == 12 || model == 310)
      d2a.writeControlTableItem(MOVING_SPEED,     id, spd);
    else
      d2a.writeControlTableItem(PROFILE_VELOCITY, id, spd);
    d2a.torqueOn(id);
  }
}

// =============================================================================
// MOTION COMPLETION HELPERS
// =============================================================================

// Returns true if ANY of the 6 servos still has its MOVING flag set.
bool isAnyServoMoving() {
  uint8_t ids[] = {1, 2, 3, 4, 5, 6};
  for (uint8_t id : ids) {
    if (d2a.readControlTableItem(MOVING, id)) return true;
  }
  return false;
}

// Block until all servos have stopped (or timeout expires), then wait an
// additional SETTLE_MS to let mechanical oscillation die out.
void waitForMotionComplete() {
  // Give servos a minimum startup window so the MOVING flag has time to assert.
  delay(KEYFRAME_INTERVAL_MS);
  unsigned long start = millis();
  while ((millis() - start) < MOTION_TIMEOUT_MS) {
    if (!isAnyServoMoving()) break;
    delay(15);  // poll interval — low enough to be responsive, not so tight
                // that it floods the bus
  }
  // Extra settle time: absorbs resonance / micro-oscillations after stop.
  delay(SETTLE_MS);
}

// =============================================================================

// Lightweight goal-position-only write. No speed or torque overhead.
// Requires prepareServosForTrajectory() to have been called first.
void sendGoalPosition(uint8_t id, float physicalDegrees) {
  RobotMotor* m = findMotor(id);
  uint16_t model = m ? m->modelNumber : 12;
  d2a.setGoalPosition(id, physicalToRaw(model, physicalDegrees));
}

// Send goal positions to all 6 servos in a SINGLE Protocol 1.0 Sync Write
// packet (instruction 0x83).  All AX-12 and MX-64A Protocol 1.0 servos share
// the same GOAL_POSITION address (30) and data width (2 bytes), so they can
// all be included in one packet — the bus carries one transaction instead of 6,
// eliminating the ~1 ms stagger between joints that sequential writes produce.
// physicals[] must be ordered: {ID1, ID2, ID3, ID4, ID5, ID6}.
void syncAllGoalPositions(float physicals[6]) {
  static const uint8_t  ids[6]    = {1, 2, 3, 4, 5, 6};
  static const uint16_t GOAL_POS_ADDR   = 30;  // same for AX-12 & MX-64A Proto1
  static const uint16_t GOAL_POS_LEN    = 2;

  uint16_t goals[6];
  for (int i = 0; i < 6; i++) {
    RobotMotor* m = findMotor(ids[i]);
    uint16_t model = m ? m->modelNumber : 12;
    goals[i] = physicalToRaw(model, physicals[i]);
  }

  DYNAMIXEL::InfoSyncWriteInst_t  sw_info;
  DYNAMIXEL::XELInfoSyncWrite_t   xel_infos[6];

  sw_info.addr             = GOAL_POS_ADDR;
  sw_info.addr_length      = GOAL_POS_LEN;
  sw_info.p_xels           = xel_infos;
  sw_info.xel_count        = 6;
  sw_info.is_info_changed  = true;

  for (int i = 0; i < 6; i++) {
    xel_infos[i].id     = ids[i];
    xel_infos[i].p_data = (uint8_t*)&goals[i];
  }

  d2a.syncWrite(&sw_info);
}

// High-level: move a motor to a logical angle (deg).
// Handles ID 2/3 mirroring automatically.
void setAngle(uint8_t id, float logicalAngle, int speed = MANUAL_SPEED) {
  executeMove(id, logicalToPhysical(id, logicalAngle), speed);

  // Mirror IDs 2 <-> 3 (physical mirrored joint pair)
  if (id == 2 || id == 3) {
    uint8_t partnerID = (id == 3) ? 2 : 3;
    executeMove(partnerID, logicalToPhysical(partnerID, 360.0 - logicalAngle), speed);
  }
}

// =============================================================================
// SEQUENCES
// =============================================================================

// 100: Interactive joint control menu — select a joint and move it continuously.
void printMainMenu() {
  PC_SERIAL.println("");
  PC_SERIAL.println("--- MAIN MENU ---");
  PC_SERIAL.println("  0   : Home all motors");
  PC_SERIAL.println("  100 : Joint control menu (1,2,4,5,6,7)");
  PC_SERIAL.println("  200 : Limp/read mode (torque off, ENTER reads positions, 999 exits)");
  PC_SERIAL.println("  555 : Play trajectory (fixed speed)");
  PC_SERIAL.println("  777 : Play MoveIt dynamic trajectory (velocity-aware)");
  PC_SERIAL.println("Enter code:");
}

// 200: All motors go limp (torque off). Press ENTER to read all servo positions.
// Type 999 and press ENTER to re-enable torque and return to the main menu.
void limpReadMode() {
  PC_SERIAL.println("\n--- LIMP / READ MODE ---");
  PC_SERIAL.println("All motors are now LIMP (torque off). Move the arm freely.");
  PC_SERIAL.println("Press ENTER to read current positions. Type 999 + ENTER to exit.");

  // Release torque on all Dynamixel joints.
  uint8_t allIds[] = {1, 2, 3, 4, 5, 6};
  for (uint8_t id : allIds) d2a.torqueOff(id);

  while (true) {
    // Block until the user sends something (even a bare newline).
    while (PC_SERIAL.available() == 0);

    // Peek at the input: if it is "999" exit, otherwise just read positions.
    String raw = PC_SERIAL.readStringUntil('\n');
    raw.trim();

    if (raw == "999") {
      PC_SERIAL.println("Exiting limp mode — re-enabling torque...");
      for (uint8_t id : allIds) d2a.torqueOn(id);
      PC_SERIAL.println("Torque ON. Returning to main menu.");
      return;
    }

    // Read and print logical (degrees) and physical (degrees) for every joint.
    PC_SERIAL.println("--- CURRENT POSITIONS ---");
    for (uint8_t id : allIds) {
      float logDeg = 0.0f, physDeg = 0.0f;
      bool ok = readPresentLogical(id, logDeg, physDeg);
      PC_SERIAL.print("  ID "); PC_SERIAL.print(id);
      if (ok) {
        PC_SERIAL.print("  logical=");     PC_SERIAL.print(logDeg,  2);
        PC_SERIAL.print(" deg  physical="); PC_SERIAL.print(physDeg, 2);
        PC_SERIAL.println(" deg");
      } else {
        PC_SERIAL.println("  (no response)");
      }
    }
    PC_SERIAL.println("--- Press ENTER for another read, or 999+ENTER to exit ---");
  }
}
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
void loop() {
  if (PC_SERIAL.available() > 0) {
    int inputCode = PC_SERIAL.parseInt();
    while (PC_SERIAL.available() > 0) PC_SERIAL.read();

    if (inputCode == 0) {
      homeAllMotors();
    } else if (inputCode == 100) {
      jointControlMenu();
    } else if (inputCode == 200) {
      limpReadMode();
    } else if (inputCode == 555) {
      playMoveitTrajectory();
      homeAllMotors();
    } else if (inputCode == 777) {
      playMoveitDynamicTrajectory();
      homeAllMotors();
    } else {
      PC_SERIAL.println("Invalid input.");
    }
    printMainMenu();
  }
}

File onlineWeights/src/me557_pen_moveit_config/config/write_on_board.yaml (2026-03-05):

board_writer:
  ros__parameters:
    # Match offline export defaults so online write_on_board runs against
    # the same world-collision assumptions.
    scene_setup_enabled: true
    scene_setup_timeout_sec: 20.0
    scene_board_enabled: true
    scene_board_id: "writing_board"
    scene_board_center_x: 0.4139  # 16.1" from base + 0.5cm half-thickness
    scene_board_center_y: 0.0
    scene_board_center_z: 0.2286
    scene_board_size_x: 0.01
    scene_board_size_y: 0.45
    scene_board_size_z: 0.40

    # ── BOARD CALIBRATION DEFAULTS (edit these 3 values) ───────────────────
    # This is the primary/default tuning path for real hardware.
    # 1) scene_board_distance_from_robot_m:
    #      moves the whole board in/out from the robot (all 4 corners X).
    #      Increase = board farther, decrease = board closer.
    # 2) scene_board_cal_tilt_vertical_deg:
    #      + top edge tips toward robot, - top edge tips away.
    # 3) scene_board_cal_tilt_horizontal_deg:
    #      + right edge tips toward robot, - left edge tips toward robot.
    scene_board_use_calibration_block: true
    scene_board_distance_from_robot_m: 0.4385 # lowered made it go further
    scene_board_cal_tilt_vertical_deg: -10.6 # negative made bottom come closer
    scene_board_cal_tilt_horizontal_deg: -4.0 # positive made right side come closer
    # --- Four-corner board definition ---
    # Corners are defined in world (base_link) frame.
    # Order: bottom-left, bottom-right, top-right, top-left
    # (left/right from the robot's perspective looking at the board)
    # Pre-filled to exactly match the current center/size config above:
    #   center=(0.4139, 0.0, 0.2286), size_y=0.45 (half=0.225), size_z=0.40 (half=0.200)
    #   Board face normal is along +X; corners lie at X = center_x = 0.4139
    scene_board_corner_bl_x: 0.4139    # bottom-left  X
    scene_board_corner_bl_y: -0.225    # bottom-left  Y  (center_y - half_width)
    scene_board_corner_bl_z:  0.0286   # bottom-left  Z  (center_z - half_height = 0.2286 - 0.200)

    scene_board_corner_br_x: 0.4139    # bottom-right X
    scene_board_corner_br_y:  0.225    # bottom-right Y  (center_y + half_width)
    scene_board_corner_br_z:  0.0286   # bottom-right Z

    scene_board_corner_tr_x: 0.4139    # top-right X
    scene_board_corner_tr_y:  0.225    # top-right Y
    scene_board_corner_tr_z:  0.4286   # top-right Z  (center_z + half_height = 0.2286 + 0.200)

    scene_board_corner_tl_x: 0.4139    # top-left X
    scene_board_corner_tl_y: -0.225    # top-left Y
    scene_board_corner_tl_z:  0.4286   # top-left Z

    # Legacy tilt fields kept for compatibility/older configs.
    # Runtime uses scene_board_cal_tilt_* as the default calibration source.
    scene_board_tilt_vertical_deg:    0.0
    scene_board_tilt_horizontal_deg:  0.0

    # Board thickness (metres) — used as the collision box depth along the normal axis
    scene_board_thickness: 0.01

    scene_table_enabled: false
    scene_table_id: "writing_table"
    scene_table_center_x: 0.0
    scene_table_center_y: -0.34
    scene_table_center_z: 0.10
    scene_table_size_x: 0.60
    scene_table_size_y: 0.60
    scene_table_size_z: 0.05

    # Use absolute board-space waypoints so the pen tip traces the full path.
    relative_to_current_pose: false
    relative_scale: 1.0
    cartesian: true
    # Balanced planning profile:
    # - Prefer Cartesian lines
    # - Allow non-Cartesian fallback only when Cartesian fails
    # - Keep a joint-span guard to reject extreme branch flips
    fallback_to_noncartesian: true
    cartesian_max_step: 0.0025
    cartesian_fraction_threshold: 0.97
    weight_orientation: 1.0
    tolerance_orientation: 0.25
    max_joint_span_rad: 1.2  # 0.8 was too tight: shoulder spans ~0.9 rad on legitimate horizontal strokes
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

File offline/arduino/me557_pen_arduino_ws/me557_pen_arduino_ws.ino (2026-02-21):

#include <Dynamixel2Arduino.h>
#include "ace_trajectory_data.h"

// Serial port connected to Dynamixel bus and host PC
#define DXL_SERIAL Serial1
#define PC_SERIAL Serial

using namespace ControlTableItem;

// Dynamixel driver instance
Dynamixel2Arduino d2a(DXL_SERIAL);

// --- GLOBAL CONFIGURATION ---
// Default speeds and smoothing parameters used when commanding servos.
const int GLOBAL_SPEED_RAW = 40;
const int SWEEP_SPEED_RAW = 60;
const int TRAJECTORY_SPEED_RAW = 40;
const int ACCEL_VAL_SMOOTH = 15;

// State for safely tucking/untucking motor 5 when motor 4 moves
float previousM5Angle = 180.0;
bool m5IsTucked = false;

// Per-motor calibration, mapping physical to logical angle ranges and offsets
struct RobotMotor {
  uint8_t id;            // Dynamixel ID
  float physicalOffset;  // Physical zero offset used to align to logical 180deg
  float lowerLimit;      // Logical lower limit (deg)
  float upperLimit;      // Logical upper limit (deg)
};

RobotMotor motors[] = {
  {1, 117.0, 120.0, 220.0},
  {2, 187.0, 120.0, 240.0},
  {3, 189.0, 120.0, 240.0},
  {4, 150.0,  40.0, 240.0},
  {5, 150.0, 100.0, 260.0},
  {6, 150.0, 140.0, 300.0}
};

const uint8_t MOVEIT_TO_SERVO_ID[5] = {1, 2, 4, 5, 6};
const char* MOVEIT_JOINT_NAMES[5] = {
  "Motor1_joint", "Motor2_L", "Motor4_elb", "Motor5_wr", "Joint_EE"
};

// --- MoveIt (radians) <-> logical (degrees) calibration ---
// These values map MoveIt joint space to the sketch's logical degree space.
// Tune once on hardware and keep consistent with the MoveIt export tool.
const float MOVEIT_HOME_RAD[5] = {
  0.0f,       // Motor1_joint -> ID1
   0.0f,    // Motor2_L     -> ID2 (ID3 mirrors via setAngle)
  0.0f,  // Motor4_elb   -> ID4
   0.0f,    // Motor5_wr    -> ID5
  0.0f        // Joint_EE     -> ID6
};
// Direction signs to correct coordinate system differences
const float MOVEIT_DIR_SIGN[5] = {-1.0f, 1.0f, 1.0f, -1.0f, 1.0f};

// --- Utility ---
// Return pointer to `RobotMotor` for the given dynamixel `id`, or nullptr.
RobotMotor* findMotor(uint8_t id) {
  for (int i = 0; i < 6; i++) {
    if (motors[i].id == id) return &motors[i];
  }
  return nullptr;
}

// Convert raw Dynamixel position units to physical degrees depending on model
float rawToPhysicalDegrees(uint16_t model, int32_t raw) {
  if (model == 12) {
    // AX-12 style 10-bit resolution over 300 deg
    return ((float)raw) * (300.0f / 1023.0f);
  }
  // e.g., XM/XH 12-bit over 360 deg
  return ((float)raw) * (360.0f / 4095.0f);
}

// Convert from this sketch's logical degrees to MoveIt joint radians
float logicalToMoveitRad(uint8_t idx, float logicalDeg) {
  const float DEG2RAD = 0.01745329252f;
  return MOVEIT_HOME_RAD[idx] +
         ((logicalDeg - 180.0f) * DEG2RAD) / MOVEIT_DIR_SIGN[idx];
}

// --- MOTION SMOOTHING ---
// Apply motion smoothing / compliance parameters appropriate for model
void applySmoothing(uint8_t id, uint16_t model) {
  if (model == 12) {
    // Older AX-style servo: use compliance settings
    d2a.writeControlTableItem(CW_COMPLIANCE_SLOPE, id, 32);
    d2a.writeControlTableItem(CCW_COMPLIANCE_SLOPE, id, 32);
    d2a.writeControlTableItem(CW_COMPLIANCE_MARGIN, id, 2);
    d2a.writeControlTableItem(CCW_COMPLIANCE_MARGIN, id, 2);
  } else {
    // Newer servos: set profile acceleration for smoother moves
    d2a.writeControlTableItem(PROFILE_ACCELERATION, id, ACCEL_VAL_SMOOTH);
  }
}

// Low-level: command a servo by physical degrees (0..360 or 0..300 depending on model)
// Ensures smoothing is applied once per servo and writes speed + goal position.
void executeMove(uint8_t id, float physicalDegrees, int speed = GLOBAL_SPEED_RAW) {
  uint16_t model = d2a.getModelNumber(id);
  static bool smoothed[11] = {false};
  if (id < 11 && !smoothed[id]) {
    applySmoothing(id, model);
    smoothed[id] = true;
  }
  d2a.writeControlTableItem(MOVING_SPEED, id, speed);
  uint16_t bitValue = (model == 12)
    ? (uint16_t)(constrain(physicalDegrees, 0, 300) * (1023.0 / 300.0))
    : (uint16_t)(constrain(physicalDegrees, 0, 360) * (4095.0 / 360.0));
  d2a.torqueOn(id);
  d2a.setGoalPosition(id, bitValue);
}

// Convert logical angle (user-facing degrees centered at 180) to physical servo degrees
// Applies per-motor limits and physical offset calibration.
float logicalToPhysical(uint8_t id, float logicalAngle) {
  RobotMotor* m = findMotor(id);
  if (!m) return logicalAngle;
  float safeLogical = constrain(logicalAngle, m->lowerLimit, m->upperLimit);
  return safeLogical + (m->physicalOffset - 180.0);
}

// Convert physical servo degrees back into logical degrees used by this sketch
float physicalToLogical(uint8_t id, float physicalAngle) {
  RobotMotor* m = findMotor(id);
  if (!m) return physicalAngle;
  return physicalAngle - (m->physicalOffset - 180.0);
}

// Read current servo position and return both logical and physical angles.
// Returns false if the servo does not respond to ping.
bool readPresentLogical(uint8_t id, float &logicalOut, float &physicalOut) {
  if (!d2a.ping(id)) return false;
  uint16_t model = d2a.getModelNumber(id);
  int32_t raw = d2a.readControlTableItem(PRESENT_POSITION, id);
  physicalOut = rawToPhysicalDegrees(model, raw);
  logicalOut = physicalToLogical(id, physicalOut);
  return true;
}

// High-level: set a motor to a `logicalAngle` (deg) while enforcing safety behaviors:
// - Tucks motor 5 when motor 4 moves into dangerous range
// - Mirrors IDs 2/3 so one follows the other for a mirrored joint pair
void setAngle(uint8_t id, float logicalAngle, int speed = GLOBAL_SPEED_RAW) {
  if (id == 5 && !m5IsTucked) previousM5Angle = logicalAngle;

  if (id == 4) {
    // If motor 4 is commanded to tuck, move M5 out of the way first
    if (logicalAngle < 70.0 && !m5IsTucked) {
      PC_SERIAL.println("!!! M4 DANGER: Tucking M5.");
      m5IsTucked = true;
      executeMove(5, logicalToPhysical(5, 100.0), speed);
      delay(800);
    }
    else if (logicalAngle >= 70.0 && m5IsTucked) {
      m5IsTucked = false;
      executeMove(5, logicalToPhysical(5, previousM5Angle), speed);
    }
  }

  executeMove(id, logicalToPhysical(id, logicalAngle), speed);

  // Mirror joint for IDs 2<->3 (physical arrangement requires mirrored values)
  if (id == 3 || id == 2) {
    uint8_t partnerID = (id == 3) ? 2 : 3;
    executeMove(partnerID, logicalToPhysical(partnerID, 360.0 - logicalAngle), speed);
  }
}

// Convert MoveIt radians to this sketch's logical degrees (inverse of above)
float moveitRadToLogical(uint8_t idx, float rad) {
  const float RAD2DEG = 57.2957795f;
  return 180.0f + MOVEIT_DIR_SIGN[idx] * (rad - MOVEIT_HOME_RAD[idx]) * RAD2DEG;
}
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

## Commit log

2026-02-10 Create individualMove.ino
    Arduino program to move the robot joints.
    Enter the motor ID, and then the degree.
    Enter 999 to go back and select a new ID.
2026-02-14 Add ME557 online ROS stack and offline Arduino version
    [Link1.STL, Link2_L.STL, Link3_R.STL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]
2026-02-14 Reorganize repo into online and offline folder structures
    [Link1.STL, Link2_L.STL, Link2_R.STL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]
2026-02-16 Simplest Possible Assembly
    CAD Model of the robot with only five moving parts. This should make the ROS sims much simpler and quicker
2026-02-17 Simple Robot V2 CAD and URDF
    [ElbowLink.STL, FixedBase.STL, PenLink.STL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]
2026-02-17 Align online/offline ACE planning and update simple_robot_v2 assets
    [Link1.STL, Link2_L.STL, Link3_R.STL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]
2026-02-21 online: servo tuning, 777 dynamic trajectory, pen servo ID7, updated README
    - robotMovements.ino: per-servo PID/compliance tuning (servo 1 & 4),
    streaming trajectory playback (code 555), velocity-aware MoveIt
    dynamic trajectory playback (code 777), PWM pen servo on pin 3 (ID 7)
    - moveItData.h: new header for code 777 dynamic trajectory
    - tools/export_moveit_dynamic.py: ROS2 node to capture MoveIt planned
    velocities + timing and write moveItData.h
    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
    [Link1.STL, Link2_L.STL, Link2_R.STL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]
2026-02-25 New URDF with Mass and Torque Properties
    [ElbowLink.STL, FixedBase.STL, PenLink.STL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]
2026-02-25 Updated URDF with Weights
    [ElbowLink.STL, FixedBase.STL, PenLink.STL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]
2026-02-26 New sims with inertia
    [ElbowLink.STL, FixedBase.STL, Link1.STL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]
